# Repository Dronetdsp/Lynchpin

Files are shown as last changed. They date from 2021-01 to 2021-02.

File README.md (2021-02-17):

# Intro
The is repo will contain all the build, scripts and params needed to build your own Lynchpin drone.

# Components

(http://www.youtube.com/watch?v=bsiZ6G9d1Ag "")

These are all the components you will need, this is not a exhaustive list, general consumables are not included (such as zip ties and heat shrink). For the most part similar alternatives can be used but motors and props should exactly match for the Lynchpin PIDs and mixer to be used. Likewise a drone of identical layout but different scale will need a new mixer.

* Flight controller - [Cube Orange](https://cubepilot.org/#/cube/features)
* Props 3x CW, 3x CCW - Gemfan 5" 3D (ZoeFPV)
* Lipos 2x - [Tattu R-Line 1050mAh 6S](https://www.genstattu.com/ta-rl3-120c-1050-6s1p.html)
* GPS - [Here2/Here2](https://cubepilot.org/#/here/here3)
* Fishing Line - braided 0.36mm/22.6kg or similar
* Recever - [FrSky - R-XSR](https://www.frsky-rc.com/product/r-xsr/)
* Motors 6x - [T-Motor F40PRO IV 1950kv](https://store-en.tmotor.com/goods.php?id=1011)
* ESCs 6x - Cloud Phoenix 50A BLHeli32 with telem pad
* Low ESR caps 6x - 50v 330uf
* PDB - [Matek Mini Power Hub](http://www.mateksys.com/?portfolio=hub5v12v)
* Standoffs 4x - M3 with bolt and nuts
* Wire - 14AWG for power and thinner for telem pads
* Bolts
    * 24x M3 14mm
    * 3x M3 10mm
    * 3x M3 washers
    * 3x M4 heat-set inserts
* ESP8266 - [Adafruit Huzzah](https://www.adafruit.com/product/2471)
* Carbon Tube 4x - [10mm OD, 9mm ID, 1m](https://www.easycomposites.co.uk/10mm-9mm-woven-finish-carbon-fibre-tube), to be cut into lengths of:
    * 4x 100mm
    * 18x 115mm
    * 6x 182mm

# 3D prints

For best results load [Frame.3mf](https://github.com/IamPete1/Lynchpin/blob/main/Frame.3mf) for pre-setup supports and layout.

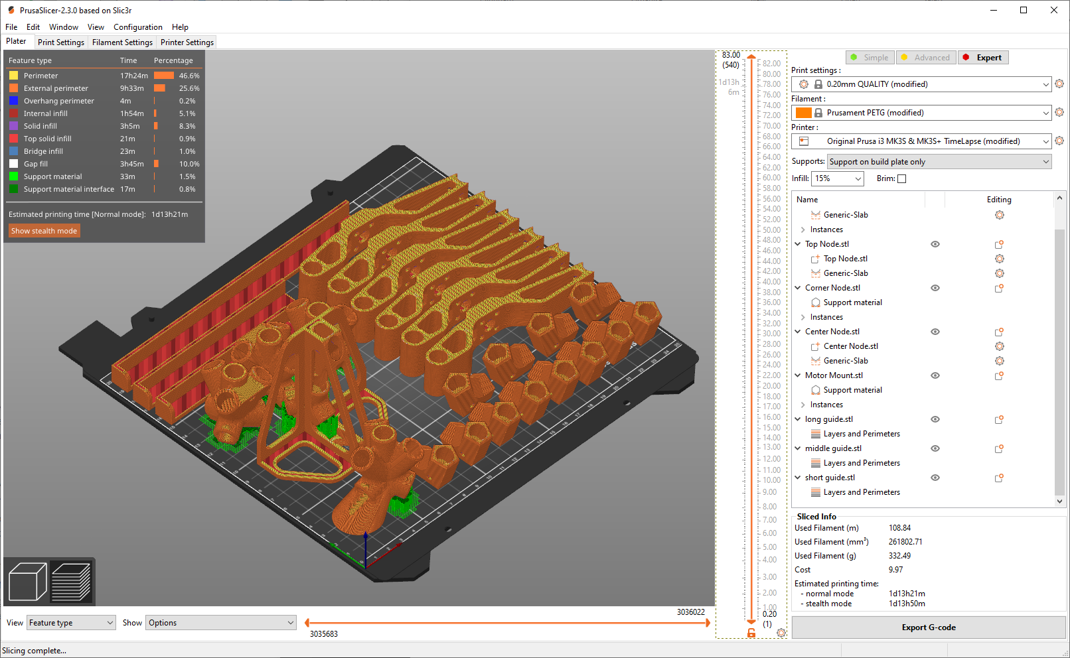
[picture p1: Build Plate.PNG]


Structural components are printed in PTEG with 5 perimeters and 15% infill. See above image for ideal layout and part orientations. Some parts require supports this should be from the build plate only and have a maximum Z height blocker such that supports are not added to the internal holes.

* [Bottom Node](https://github.com/IamPete1/Lynchpin/blob/main/STLs/Bottom%20Node.stl) x 3 - requires support
* [Top Node](https://github.com/IamPete1/Lynchpin/blob/main/STLs/Top%20Node.stl) - requires support
* [Center Node](https://github.com/IamPete1/Lynchpin/blob/main/STLs/Center%20Node.stl) - requires support
* [Corner Node](https://github.com/IamPete1/Lynchpin/blob/main/STLs/Corner%20Node.stl) x 12
* [Motor Mount](https://github.com/IamPete1/Lynchpin/blob/main/STLs/Motor%20Mount.stl) x 6

Optional, but very useful, tube cutting guides can be printed from any material with standard settings.
* [Long](https://github.com/IamPete1/Lynchpin/blob/main/STLs/long%20guide.stl) (182mm)
* [Medium](https://github.com/IamPete1/Lynchpin/blob/main/STLs/middle%20guide.stl) (115mm)
* [Short](https://github.com/IamPete1/Lynchpin/blob/main/STLs/short%20guide.stl) (100mm)

# Laser Cut

The base plate is designed for laser cutting, any material of about 3mm thickness, Acriylic looks cool. Alternatively the plate can be printed.
* [Base - DXF](https://github.com/IamPete1/Lynchpin/blob/main/base%20plate.dxf)
* [Base - STL](https://github.com/IamPete1/Lynchpin/blob/main/STLs/Base%20Plate.stl)

# Building the frame

(http://www.youtube.com/watch?v=Yiew8CDSbIk "")

# Wiring

(http://www.youtube.com/watch?v=npzUJ9enRJU "")

[Cube Pinouts](https://docs.cubepilot.org/user-guides/autopilot/the-cube-module-overview)

[Flashing the ESP8266 for WiFi telemetry](https://ardupilot.org/copter/docs/common-esp8266-telemetry.html)

Close up pictures:

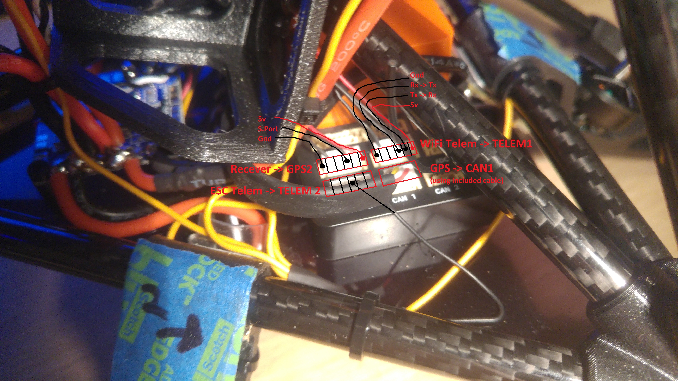
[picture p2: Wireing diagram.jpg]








# ArduPilot setup

ArduPilot setup is much like a normal copter. Param set [here](https://github.com/IamPete1/Lynchpin/blob/main/Lynchpin%20CubeOrange.param). You will also need a [lua script](https://github.com/IamPete1/Lynchpin/blob/main/Motors_6DoF_LynchPin.lua) to tell AP the location and directions of each motor. Optionally an [additional script](https://github.com/IamPete1/Lynchpin/tree/main/scripts) can be added to give control over the roll and pitch axis.

(http://www.youtube.com/watch?v=iq5y_lpEIGQ "")

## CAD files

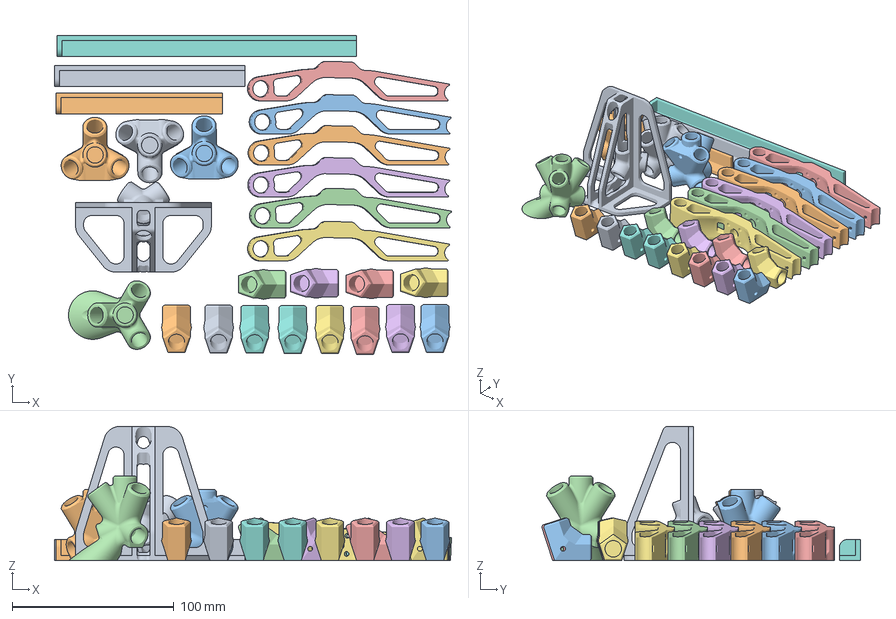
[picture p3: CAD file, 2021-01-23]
Frame.3mf
245.7 x 197.1 x 83.0 mm
Bottom Node.stl
Top Node.stl
Corner Node.stl
Center Node.stl
Motor Mount.stl
long guide.stl
middle guide.stl
short guide.stl

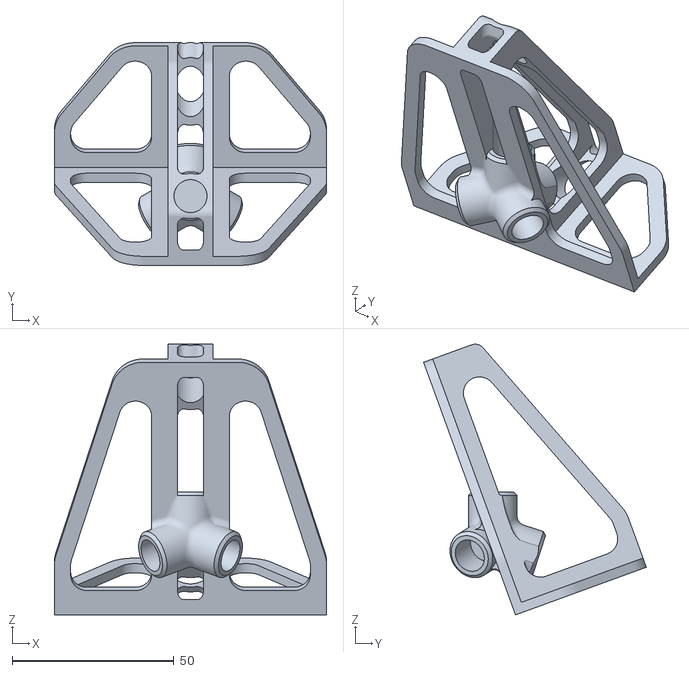
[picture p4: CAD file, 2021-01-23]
STLs/Center Node.stl
84.0 x 68.8 x 83.6

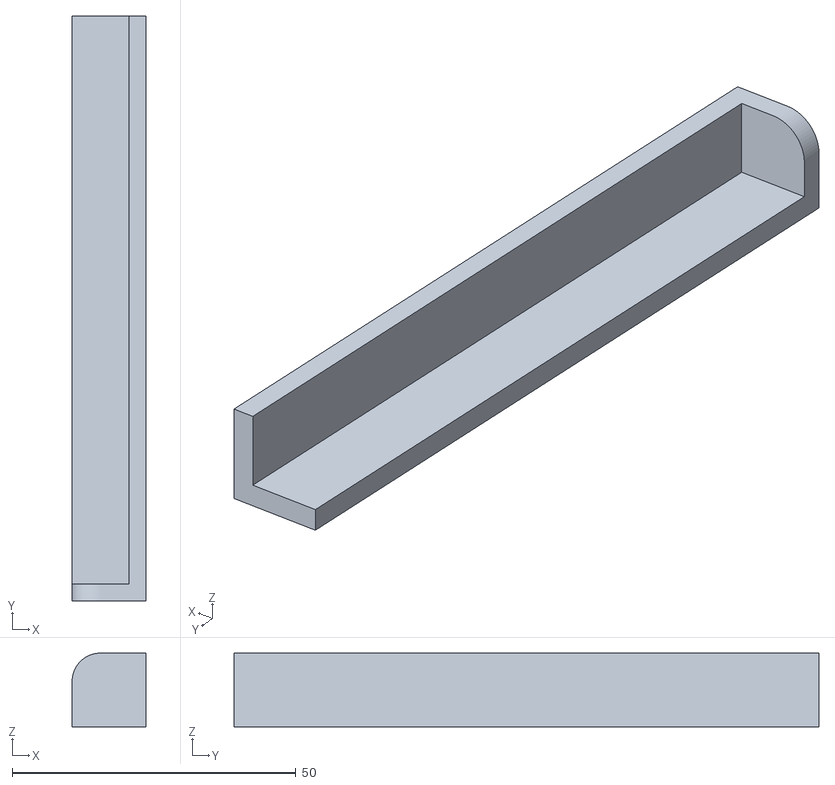
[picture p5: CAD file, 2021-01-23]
STLs/short guide.stl
13.0 x 103.0 x 13.0

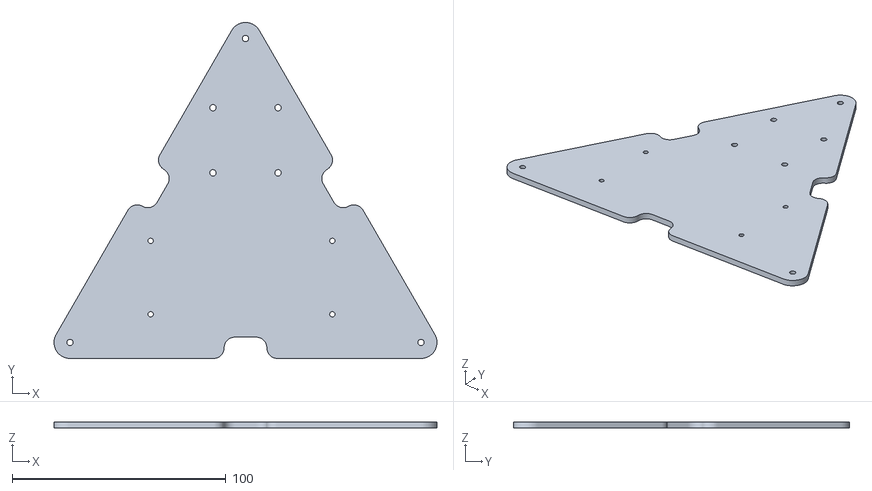
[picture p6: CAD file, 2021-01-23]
STLs/Base Plate.stl
179.3 x 157.3 x 3.00

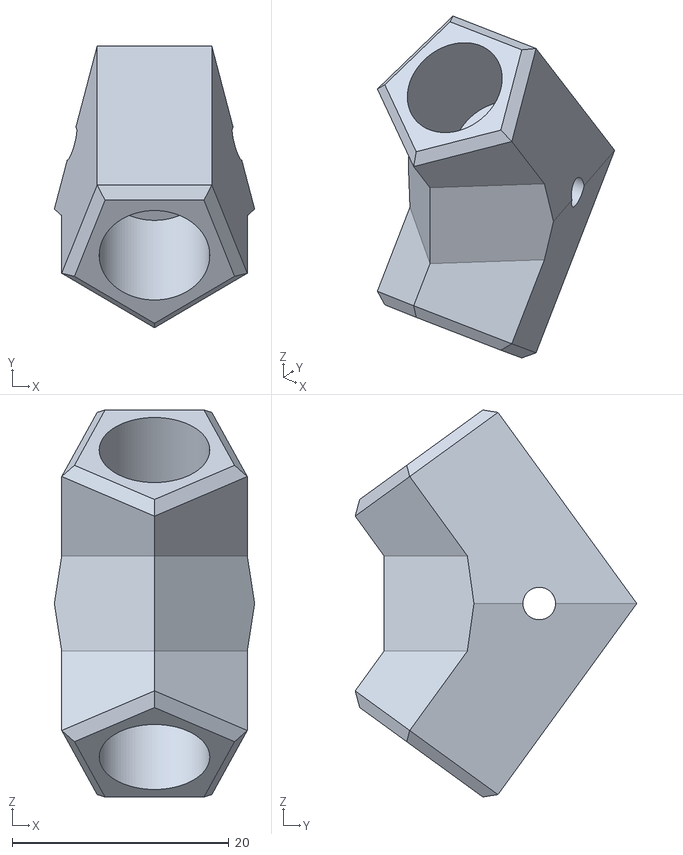
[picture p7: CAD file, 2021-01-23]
STLs/Corner Node.stl
18.5 x 26.0 x 35.7

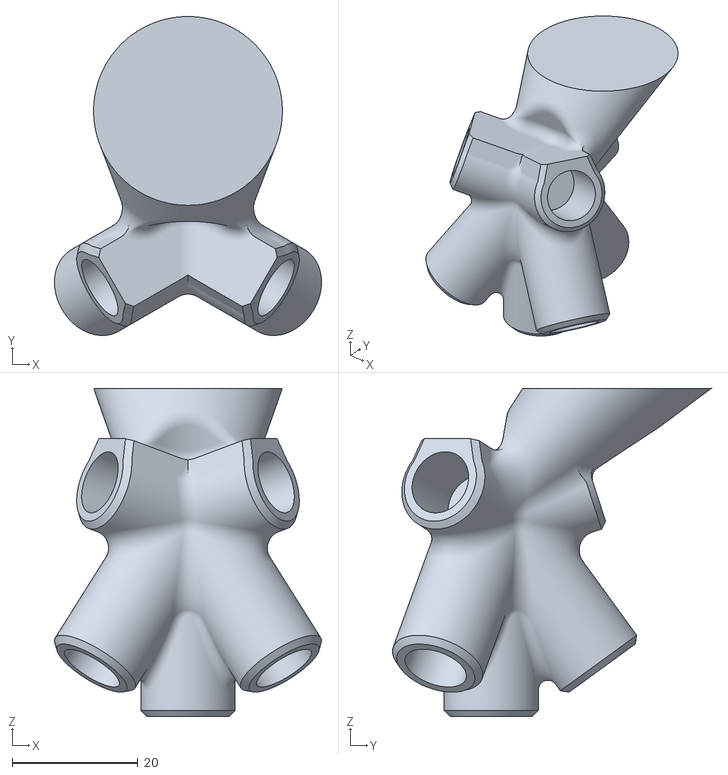
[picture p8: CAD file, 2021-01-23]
STLs/Top Node.stl
42.4 x 50.7 x 52.2

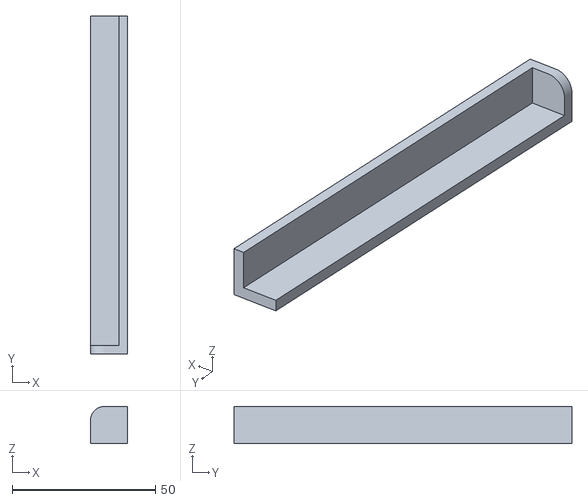
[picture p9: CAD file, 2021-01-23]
STLs/middle guide.stl
13.0 x 118.0 x 13.0

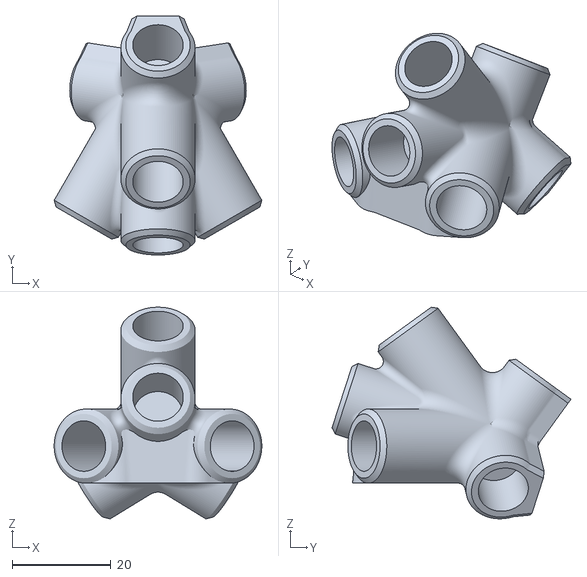
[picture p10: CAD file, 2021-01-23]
STLs/Bottom Node.stl
42.0 x 48.3 x 42.8

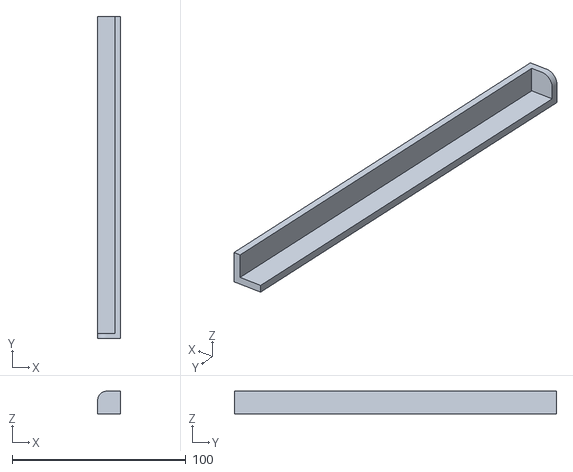
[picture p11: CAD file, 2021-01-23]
STLs/long guide.stl
13.0 x 185.3 x 13.0

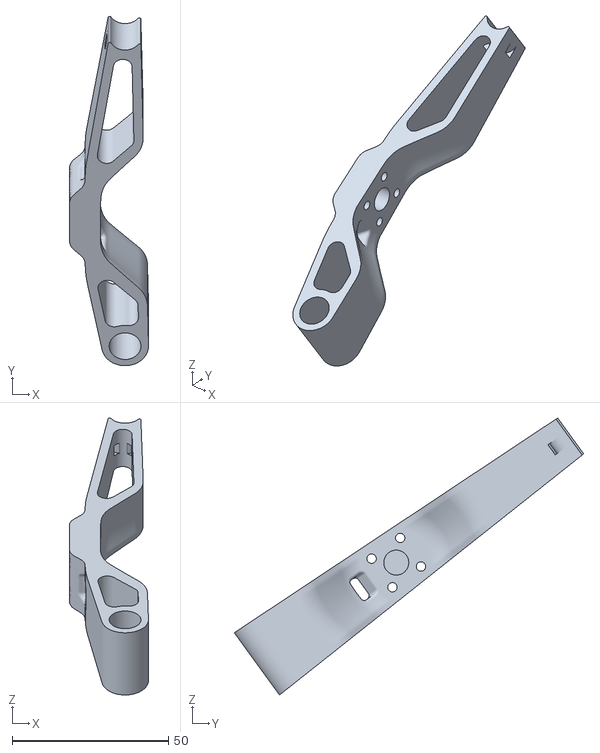
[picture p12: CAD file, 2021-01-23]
STLs/Motor Mount.stl
25.3 x 111.9 x 88.7

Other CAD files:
base plate.dxf

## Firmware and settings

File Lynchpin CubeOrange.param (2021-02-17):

AHRS_ORIENTATION,2
ATC_ANGLE_BOOST,0
ATC_RAT_PIT_D,0.005
ATC_RAT_PIT_I,0.2
ATC_RAT_PIT_P,0.2
ATC_RAT_RLL_D,0.005
ATC_RAT_RLL_I,0.2
ATC_RAT_RLL_P,0.2
ATC_RAT_YAW_D,0.004
ATC_RAT_YAW_FLTD,20
ATC_RAT_YAW_FLTE,0
ATC_RAT_YAW_I,0.15
ATC_RAT_YAW_P,0.15
BATT_CAPACITY,2100
BATT_LOW_VOLT,21
BATT_MONITOR,9
BRD_PWM_COUNT,6
BRD_SAFETYENABLE,0
CAN_D2_PROTOCOL,0
CAN_P1_DRIVER,1
COMPASS_USE,1
COMPASS_USE2,0
COMPASS_USE3,0
DISARM_DELAY,0
FLTMODE1,0
FLTMODE2,2
FLTMODE3,5
FLTMODE4,0
FLTMODE5,2
FLTMODE6,5
FRAME_CLASS,16
FS_CRASH_CHECK,0
GPS_TYPE,9
INS_GYRO_FILTER,50
INS_HNTCH_ENABLE,1
INS_HNTCH_MODE,3
INS_HNTCH_REF,1
LOG_BITMASK,180222
MOT_BAT_VOLT_MAX,26.4
MOT_BAT_VOLT_MIN,21
MOT_PWM_TYPE,5
MOT_SPIN_MAX,1
MOT_THST_EXPO,0.67
MOT_YAW_HEADROOM,50
NTF_LED_TYPES,231
RC8_OPTION,31
RC9_OPTION,300
RC13_OPTION,301
RC15_OPTION,302
RSSI_TYPE,3
SCR_ENABLE,1
SERIAL1_BAUD,921
SERIAL2_PROTOCOL,16
SERIAL3_PROTOCOL,-1
SERIAL4_OPTIONS,15
SERIAL4_PROTOCOL,23
SERVO_BLH_MASK,16128
SERVO_BLH_OTYPE,5
SERVO_BLH_REMASK,16128
SERVO9_FUNCTION,33
SERVO10_FUNCTION,34
SERVO11_FUNCTION,35
SERVO12_FUNCTION,36
SERVO13_FUNCTION,37
SERVO14_FUNCTION,38
TERRAIN_ENABLE,0

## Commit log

2021-01-23 Add files and update readme
    [Base Plate.stl, Bottom Node.stl, Center Node.stl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]
2021-02-17 Add param set and scripts
    [Lynchpin CubeOrange.param]
